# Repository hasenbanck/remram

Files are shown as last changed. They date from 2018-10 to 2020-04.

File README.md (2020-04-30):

# RemRam - 3D printer controller

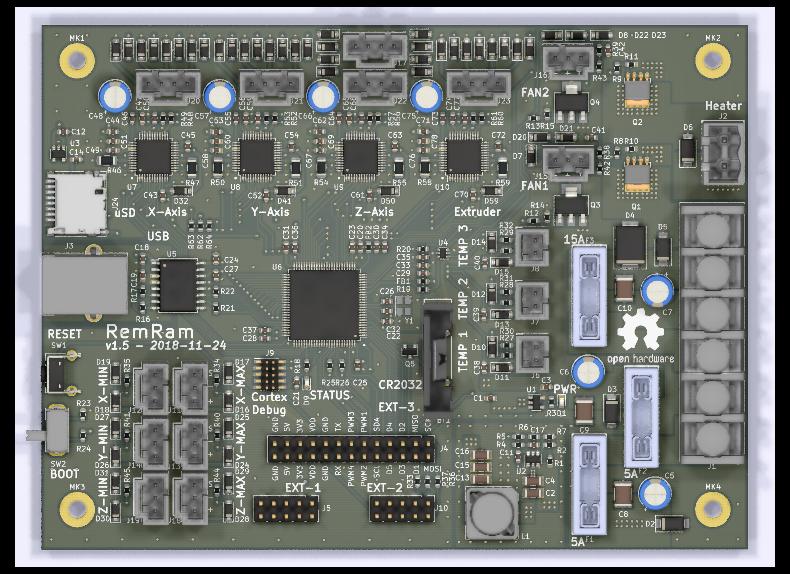
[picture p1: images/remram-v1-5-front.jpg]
RemRam v1.5


## Features

 * 32bit STM32F765VI
   * 216 MHz
   * 512 KBytes RAM
   * 2 MBytes flash
 * 4x TMC2130 stepper driver
   * stealthChop
   * spreadCycle
   * coolStep
   * stallGuard
 * 24V main power rail
   * heatbed output (15A)
   * heater output (5A)
   * stepper driver and logic (5A)
 * 5V secondary power rail (3A)
   * FAN1 and FAN2
 * 2x 3.3V tertiary power rail (2x 0.5A)
   * MCU power (IO)
   * SD card power
 * Robust connectors
 * Quality, high powered MOSFET
 * 4 layer board with single side component placement

## PCB design

Software used KiCad 5.0

### Alternative Parts

You can substitute the TPS5408 with a TPS5402. In this case you also need to replace R4 with a Zero Ohm resistor.

## Compiling the firmware

 1. [Install Arduino](https://www.arduino.cc/en/Main/Software)
 2. [Install the STM32 Core](https://github.com/stm32duino/wiki/wiki/Getting-Started)
 3. Optional for Serial over USB support: [Update the STM32 Core using the git repository](https://github.com/stm32duino/wiki/wiki/Using-git-repository)
 4. [Download the current git branch of Marlin 2.0](https://github.com/MarlinFirmware/Marlin/tree/bugfix-2.0.x)
 5. Open the Marlin project, select the "RemRam V1" board from the Marlin menue, edit the Marlin configuration file and build the project. You need to find the HEX or BIN file that Arduino creates and flash the firmware onto the board (See: "How to flash the firmware").

## Configure Marlin

These are the board specific ```Configuration.h``` changes:
```C
#define SERIAL_PORT 1 // 1 = UART connection on EXT3
                      // -1 = Serial over USB (see: Virtual COM Port Support (Serial over USB))
                      // You can also configure SERIAL_PORT_2

#define BAUDRATE 115200 // 115200 for UART on EXT3
                        // 1000000 for Serial over USB

#define MOTHERBOARD BOARD_REMRAM_V1

#define X_DRIVER_TYPE  TMC2130
#define Y_DRIVER_TYPE  TMC2130
#define Z_DRIVER_TYPE  TMC2130
#define E0_DRIVER_TYPE TMC2130

#define ENDSTOP_INTERRUPTS_FEATURE

#define SDSUPPORT
```

These are the board specific ```Configuration_adv.h``` changes:
```C
#define MINIMUM_STEPPER_DIR_DELAY 20
#define MINIMUM_STEPPER_PULSE 0
#define MAXIMUM_STEPPER_RATE 400000

#if HAS_TRINAMIC

  // You can change ever value EXCEPT R_SENSE based on your setup.
  // Example values of my HEVO setup

  #define R_SENSE           0.12  // DO NOT CHANGE! Need to be 0.12 for RemRam V1
  #define HOLD_MULTIPLIER    0.3  // Scales down the holding current from run current
  #define INTERPOLATE       true  // Interpolate X/Y/Z_MICROSTEPS to 256

  #define X_CURRENT          750  // rms current in mA. Multiply by 1.41 for peak current.
  #define X_MICROSTEPS       256  // 0..256

  #define Y_CURRENT          750
  #define Y_MICROSTEPS       256

  #define Z_CURRENT          750
  #define Z_MICROSTEPS       256

  #define E0_CURRENT         400
  #define E0_MICROSTEPS      256

  #define STEALTHCHOP
  #define MONITOR_DRIVER_STATUS

  #if ENABLED(MONITOR_DRIVER_STATUS)
    #define CURRENT_STEP_DOWN     50  // [mA]
    #define REPORT_CURRENT_CHANGE
    #define STOP_ON_ERROR
  #endif

  #define SENSORLESS_HOMING // If you want to use sensorless homing

  #if ENABLED(SENSORLESS_HOMING) || ENABLED(SENSORLESS_PROBING)
    #define X_STALL_SENSITIVITY  2
    #define Y_STALL_SENSITIVITY  2
    #define Z_STALL_SENSITIVITY  2
  #endif

  #define TMC_DEBUG // Helpfull when setting up your system

#endif
```

```src/pins/pins_REMRAM_V1.h```
```C
// Use only one or the other (you could damage the hardware otherwise!)
#define SDSS               57   // Onboard SD card reader
//#define SDSS              9   // LCD SD card reader
```

Of course you need to aditionally change the configuration files based on your particular printer setup.

## Virtual COM Port Support (Serial over USB)

Virtual COM Port (also known as VCOM or CDC) support will land in the "official" STM32 arduino core with version 1.5.0. If you want to use VCOM feature earlier, you can use the the [master branch of the offical core](https://github.com/stm32duino/Arduino_Core_STM32).

Have a look at the "[Update the STM32 Core using the git repository](https://github.com/stm32duino/wiki/wiki/Using-git-repository)" on how to update the STM32 arduino core with a custom git branch. You also have to select "CDC Full Speed" as USB interface inside Arduino to enable the CDC interface.

## External SD card reader

Most RepRapDiscount based LCD modules come with an integrated SD card reader. You can use this reader, but because this system is 3.3V based, the signal to noise ration is higher. Meaning you will need a much better connection between the LCD module and the board. Crappy ribbon cables won't do it in most cases. Dropping the SPI speed AND using shielded ribbon cables is most likely needed to get a good signal integrity.

You can't use the onboard SD card reader and the LCD card reader at the same time. DO NOT insert a SD card in both slots at the same time, because this could lead to a hardware failure.

## How to flash the firmware

Supported:

 * Using the Cortex Debug Header (SWD)
 * Using DFU over USB
 * Using UART on EXT-3 PIN 15 (TX) and PIN 16 (RX)

### Cortex Debug Header

You can use the Cortex Debug Header to program the STM32 firmware and do step-by-step debugging.

This board only support SWD. SWO is not routed to the header, since we had to use the
pin for a PWM output.

I personally use the SEGGER J-Link Edu Mini. But any 2€ Ebay flasher should work ("ST Link V2").
Please make sure that you have a adapter for the debug header!

The debug header is a 2x05 pin (1.27/0.05”).

### DFU (USB)

https://www.st.com/en/development-tools/stsw-stm32080.html

Please pay attention that you don't just flash the HEX/BIN file, but the special DFU image file (*.dfu) you need to create with the "DFU file manager" tool. DfuSe will let you happily flash a HEX/BIN file, but the board won't boot without a propper DFU file.

Please read the "UM0412" user manual you can find at the above link.

### UART

https://www.st.com/en/development-tools/flasher-stm32.html

## LICENSE

CERN OHL version 1.2

The files under PCB/packages3d are excluded from this license and are provided under fair use terms for this open-source project.

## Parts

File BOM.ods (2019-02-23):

Reference(s) | Value | Mft. Nr. | Digikey Nr. | Mouser Nr. | Qty | Notice | Footprint | Datasheet
BT1 | S8401-46 | S8401-46 | 952-1743-1-ND | 855-S8401-46 | 1 |  | custom-footprints:VBH2032-1 | https://www.mouser.de/datasheet/2/346/VBH2032-1_new-258024.pdf
C1, C3, C12, C14, C50, C59, C68, C77 | 10uF | GRM188R61A106KE69J | 490-14372-1-ND | 81-ZRB18AR61E106ME1L | 8 | Min. 10V | Capacitor_SMD:C_0603_1608Metric | ~
C11, C18, C19, C21, C22, C23, C24, C25, C27, C28, C31, C33, C34, C35, C38, C39, C40, C41, C42, C43, C44, C45, C49, C51, C52, C53, C54, C58, C60, C61, C62, C63, C67, C69, C70, C71, C72, C76, C78 | 100nF | C0603C104M5RACTU | 399-7845-1-ND | 80-C0603C104M5R | 39 | Min. 35V | Capacitor_SMD:C_0603_1608Metric | ~
C13, C15, C16 | 22uF | GRM319C80J226ME15D | 1276-3148-1-ND | 81-GRM319C80J226ME5D | 3 | Min. 10V | Capacitor_SMD:C_1206_3216Metric | ~
C17 | 75pF | GRM1885C1H750JA01D | 490-1424-1-ND | 81-GRM1885C1H750JA | 1 | Min. 10 V | Capacitor_SMD:C_0603_1608Metric | ~
C2 | 10uF | GRM319R6YA106KA12D | 490-12425-1-ND | 81-GRT31CC8YA106ME1L | 1 | Min. 35V | Capacitor_SMD:C_1206_3216Metric | ~
C20 | 4.7uF | GRM188R61A475ME15D | 490-10478-1-ND | 810-CGB3B1X5R1A475MC | 1 | Min. 10V | Capacitor_SMD:C_0603_1608Metric | ~
C26, C32 | 8pF | GCM1885C1H8R0DA16D | 490-14528-1-ND | 81-GCM1885C1H8R0DA6D | 2 | Min. 10V | Capacitor_SMD:C_0603_1608Metric | ~
C29, C30 | 1uF | 885012206052 | 732-7971-1-ND | 710-885012106010 | 2 | Min. 10V | Capacitor_SMD:C_0603_1608Metric | ~
C36, C37 | 2.2uF | 885012106011 | 732-7908-1-ND | 710-885012106011 | 2 | Min. 10V | Capacitor_SMD:C_0603_1608Metric | ~
C4 | 100nF | C1206C104K5RACAUTO | 399-7009-1-ND | 80-C1206C104K5RAUTO | 1 | Min. 35V | Capacitor_SMD:C_1206_3216Metric | ~
C46, C55, C64, C73 | 22nF | 885012206091 | 732-8009-1-ND | 710-885012206091 | 4 | Min. 50V | Capacitor_SMD:C_0603_1608Metric | ~
C47, C56, C65, C74 | 470nF | 885012106008 | 732-7905-1-ND | 710-885012106008 | 4 | Min. 10V | Capacitor_SMD:C_0603_1608Metric | ~
C5, C6, C7, C48, C57, C66, C75 | 100uF | 860020573008 | 732-8942-1-ND | 710-860020573008 | 7 | Min. 35V | Capacitor_THT:CP_Radial_D6.3mm_P2.50mm | https://eu.mouser.com/datasheet/2/293/e-uvz-1219460.pdf
C8, C9, C10 | 100nF | C4532X7R2J104K230KA | 445-2300-1-ND | 603-CC812KKX7R9BB104 | 3 | Min. 35V | Capacitor_SMD:C_1812_4532Metric | ~
D1 | LTST-C194KGKT | LTST-C194KGKT | 160-1834-1-ND | 859-LTST-C194KGKT | 1 |  | LED_SMD:LED_0603_1608Metric | ~
D2, D3 | SMAJ28A | SMAJ28A-13-F | SMAJ28A-FDICT-ND | 621-SMAJ28A-13-F | 2 |  | Diode_SMD:D_SMA | https://www.mouser.de/datasheet/2/240/Littelfuse_TVS_Diode_SMAJ_Datasheet.pdf-540740.pdf
D32, D33, D34, D35, D36, D37, D38, D39, D40, D41, D42, D43, D44, D45, D46, D47, D48, D49, D50, D51, D52, D53, D54, D55, D56, D57, D58, D59, D60, D61, D62, D63, D64, D65, D66, D67 | S310FA | S310FA | S310FACT-ND | 512-S310FA | 36 |  | Diode_SMD:D_SOD-123 | https://www.mouser.com/ds/2/149/S310FA-888043.pdf
D4 | S3A-13-F | S3A-13-F | S3A-FDICT-ND | 621-S3A-F | 1 |  | Diode_SMD:D_SMC | https://www.mouser.de/datasheet/2/115/ds16005-37880.pdf
D5, D6 | SK310A-LTP | SK310A-LTP | SK310A-LTPMSCT-ND | 833-SK310A-LTP | 2 |  | Diode_SMD:D_SMA | https://www.mouser.de/ProductDetail/Micro-Commercial-Components-MCC/SK310A-TP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
D7, D8, D10, D11, D12, D13, D14, D15, D16, D17, D18, D19, D20, D21, D22, D23, D24, D25, D26, D27, D28, D29, D30, D31 | BAT54GWJ | BAT54GWJ | 1727-7328-1-ND | 841-BAT54GWJ | 24 |  | Diode_SMD:D_SOD-123 | https://www.mouser.de/datasheet/2/916/BAT54GW-1318921.pdf
D9 | LTST-C194KSKT | LTST-C194KSKT | 160-1836-1-ND | 859-LTST-C194KSKT | 1 |  | LED_SMD:LED_0603_1608Metric | ~
F1, F2, F3 | 3557-2 | 3557-2 | 36-3557-2-ND | 534-3557-2 | 3 |  | custom-footprints:KEYSTONE-FUSE-3557-2 | https://www.mouser.de/datasheet/2/215/557-2-744839.pdf
FB1, FB2 | MPZ1608S221A | MPZ1608S221A | 445-1565-1-ND | 810-MPZ1608S221A | 2 |  | Resistor_SMD:R_0603_1608Metric | https://www.mouser.de/datasheet/2/400/eads_commercial_power_mpz1608_en-923650.pdf
J1 | 4DB-P108-06 | 4DB-P108-06 | A98476-ND | 571-214376679 | 1 | Alternative OSTYK42106030? | custom-footprints:4DB-P108-06
J11, J12, J13, J14, J15, J16, J18, J19 | 70543-0002 | 70543-0002 | WM4801-ND | 538-70543-0002 | 8 |  | custom-footprints:70543-0002 | ~
J17, J20, J21, J22, J23 | 70543-0003 | 70543-0003 | WM4802-ND | 538-70543-0003 | 5 |  | custom-footprints:70543-0003 | https://www.mouser.de/ProductDetail/Molex/70543-0003
J2 | 039531-1002 | 039531-1002 | WM7837-ND | 538-39531-1002 | 1 |  | custom-footprints:39531-1002 | ~
J24 | DM3D-SF | DM3D-SF | HR1941CT-ND | 798-DM3D-SF | 1 |  | custom-footprints:microSD_HC_Hirose_DM3D-SF | ~
J3 | 67068-8000 | 67068-8000 | WM17113-ND | 538-67068-8000 | 1 |  | custom-footprints:67068-8000 | https://www.mouser.de/datasheet/2/276/0670688000_IO_CONNECTORS-172066.pdf
J4 | Conn_02x13_Odd_Even | 67997-426HLF | 609-3246-ND | 649-67997-426HLF | 1 |  | custom-footprints:PinHeader_2x13_P2.54mm_Vertical | ~
J5, J10 | Conn_02x05 | 67997-210HLF | 609-3236-ND | 649-67997-210HLF | 2 | Buy them cheap on aliexpress, ebay or amazon | Connector_PinHeader_2.54mm:PinHeader_2x05_P2.54mm_Vertical
J6, J7, J8 | 70543-0001 | 70543-0001 | WM4800-ND | 538-70543-0001 | 3 |  | custom-footprints:70543-0001 | https://www.mouser.de/ProductDetail/Molex/50-57-9402
J9 | 20021121-00010C4LF | 20021121-00010C4LF | 609-3695-1-ND | 649-202112100010C4LF | 1 |  | custom-footprints:PinHeader_2x05_P1.27mm_Vertical | https://www.mouser.de/datasheet/2/445/6220xx21121-542317.pdf
L1 | 18uH | 7447798181 | 732-2417-1-ND | 710-7447798181 | 1 |  | custom-footprints:L_Wuerth_WE-PDF | https://www.mouser.com/datasheet/2/445/7447798181-539715.pdf
Q1, Q2 | PSMN1R2-30YLC,115 | PSMN1R2-30YLC,115 | 1727-5295-1-ND | 771-PSMN1R230YLC115 | 2 | Alternatives: PSMN1R8-40YLC,115; PSMN1R3-30YL,115 | custom-footprints:SOT-669_LFPAK_ThermalVias-1 | https://assets.nexperia.com/documents/data-sheet/PSMN1R2-30YLC.pdf
Q3, Q4 | BUK9840-55 | BUK9840-55/CUX | 1727-2227-1-ND | 771-BUK9840-55/CUX | 2 |  | Package_TO_SOT_SMD:SOT-223-3_TabPin2 | https://www.mouser.de/datasheet/2/916/BUK9840-55-1320170.pdf
Q5 | IRLML6401 | IRLML6401TRPBF | IRLML6401PBFCT-ND | 942-IRLML6401TRPBF | 1 | Alternative: SI2333DS-T1-E3 | Package_TO_SOT_SMD:SOT-23 | https://www.infineon.com/dgdl/irlml6401pbf.pdf?fileId=5546d462533600a401535668b96d2634
R1 | 511k | ERJ-3EKF5113V | P511KHCT-ND | 667-ERJ-3EKF5113V | 1 |  | Resistor_SMD:R_0603_1608Metric | ~
R6, R10, R11, R14, R15 | 100k | CRCW0603100KFKEAC | 541-3950-1-ND | 71-CRCW0603100KFKEAC | 5 |  | Resistor_SMD:R_0603_1608Metric | ~
R8, R9, R12, R13, R16, R17, R21, R22, R33, R36, R37 | 100 | RC0603FR-7W100RL | YAG3561CT-ND | 603-RC0603FR-7W100RL | 11 |  | Resistor_SMD:R_0603_1608Metric | ~
R3, R18, R19, R20, R34, R35, R40, R41, R44, R45 | 1k | RC0603JR-7W1KL | YAG2323CT-ND | 603-RC0603JR-7W1KL | 10 |  | Resistor_SMD:R_0603_1608Metric | ~
R2 | 105k | ERJ-3EKF1053V | P105KHCT-ND | 667-ERJ-3EKF1053V | 1 |  | Resistor_SMD:R_0603_1608Metric | ~
R23, R24, R48, R49, R52, R53, R56, R57, R60, R61, R62, R63, R64 | 47k | CR0603-FX-4702ELF | CR0603-FX-4702ELFTR-ND | 652-CR0603FX-4702ELF | 13 |  | Resistor_SMD:R_0603_1608Metric | ~
R25, R26 | 10k | AC0603FR-0710KL | P10.0KHCT-ND | 603-AC0603FR-0710KL | 2 |  | Resistor_SMD:R_0603_1608Metric | ~
R27, R28, R29, R30, R31, R32, R38, R39, R42, R43, R65 | 4.7k | AC0603JR-074K7L | YAG3676CT-ND | 603-AC0603JR-074K7L | 11 |  | Resistor_SMD:R_0603_1608Metric | ~
R4 | 2k | CRCW06032K00FKEAC | 541-3953-1-ND | 71-CRCW06032K00FKEAC | 1 | Option when using TPS54302: ERJ-3GEY0R00V | Resistor_SMD:R_0603_1608Metric | ~
R46, R47, R50, R51, R54, R55, R58, R59 | 0.12 | ERJ-8RSJR12V | P.12PCT-ND | 667-ERJ-8RSJR12V | 8 |  | Resistor_SMD:R_1206_3216Metric | https://www.mouser.de/ProductDetail/IRC-TT-Electronics/LRC-LR1206LF-01-R120-F
R5 | 49.9 | ERJ-3EKF49R9V | P49.9HCT-ND | 667-ERJ-3EKF49R9V | 1 |  | Resistor_SMD:R_0603_1608Metric | ~
R7 | 13.3k | AC0603FR-0713K7L | P13.7KHCT-ND | 603-AC0603FR-0713K7L | 1 |  | Resistor_SMD:R_0603_1608Metric | ~
SW1 | PTS645VL39-2 | PTS645VL392LFS | CKN9103-ND | 611-PTS645VL392 | 1 |  | Button_Switch_THT:SW_Tactile_SPST_Angled_PTS645Vx39-2LFS | https://www.mouser.de/datasheet/2/60/-1131575.pdf
SW2 | OS102011MA1QN1 | OS102011MA1QN1 | CKN9559-ND | 611-OS102011MA1QN1 | 1 |  | custom-footprints:SW_CuK_OS102011MA1QN1_SPDT_Angled | ~
U1, U3 | AP7365-33WG-7 | AP7365-33WG-7 | AP7365-33WG-7DICT-ND | 621-AP7365-33WG-7 | 2 |  | Package_TO_SOT_SMD:SOT-23-5 | https://www.mouser.de/datasheet/2/115/AP7365-86154.pdf
U7, U8, U9, U10 | TMC2130-TA | TMC2130-TA-T | 1460-1186-1-ND |  | 4 | Not available at Mouser | custom-footprints:TQFP-48-1EP_7x7mm_P0.5mm_EP4.8x4.8mm-Heatsink | https://www.trinamic.com/fileadmin/assets/Products/ICs_Documents/TMC2130_datasheet.pdf
U2 | TPS54308 | TPS54308DDCT | 296-47881-1-ND | 595-TPS54308DDCT | 1 | Alternative: TOS54302 (Attention R4!) | Package_TO_SOT_SMD:SOT-23-6 | http://www.ti.com/lit/ds/symlink/tps54308.pdf
U4 | SN74LVC2G17DCKR | SN74LVC2G17DCKR | 296-13013-1-ND | 595-SN74LVC2G17DCKR | 1 |  | Package_TO_SOT_SMD:SOT-363_SC-70-6 | http://www.ti.com/lit/sg/scyt129e/scyt129e.pdf
U5 | ADUM4160 | ADUM4160 | ADUM4160BRIZ-RLCT-ND | 584-ADUM4160BRWZ-R | 1 |  | Package_SO:SOIC-16W_7.5x10.3mm_P1.27mm | http://www.analog.com/media/en/technical-documentation/data-sheets/ADuM4160.pdf
U6 | STM32F765VIT6 | STM32F765VIT6 | 497-16631-ND | 511-STM32F765VIT6 | 1 |  | custom-footprints:TQFP-100_14x14mm_P0.5mm | http://www.st.com/en/microcontrollers/stm32f765vi.html
Y1 | TSX-3225 24.0000MF15X-AC3 | TSX-3225 24.0000MF15X-AC3 | SER3635CT-ND | 732-TX325-24F15X-AC3 | 1 |  | Crystal:Crystal_SMD_SeikoEpson_TSX3225-4Pin_3.2x2.5mm | https://www5.epsondevice.com/en/products/crystal_unit/tsx3225.html

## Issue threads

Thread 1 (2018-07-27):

Write the STM32F7 HAL for Marlin 2.0

hasenbanck, 2018-07-27:
Even though there is already a STM32F7 HAL in Marlin 2.0 it is based on an unmaintained Arduino driver (https://github.com/danieleff/STM32GENERIC).

We should use the official arduino core (https://github.com/stm32duino/Arduino_Core_STM32) for the HAL. A current implementation is available (https://github.com/hasenbanck/Arduino_Core_STM32). It should move into upstream "soon".

Since the current STM32F7 HAL in Marlin is pretty board specific and can be highly simplified using the official Arduino core from ST, we should replace the current STM32F7 HAL in the long run. Right now it might be best to simply open a new HAL folder (STM32F7ng?).

hasenbanck, 2018-07-27:
It seems that another developer ported the F4 HAL for the official arduino core. We should use his code and maybe even consider making a unified HAL altogether.

https://github.com/ghent360/Marlin/tree/bugfix-2.0.x/Marlin/src/HAL/HAL_STM32F4

hasenbanck, 2018-07-27:
Forget this. The official F4 HAL is already ported for the official core.

hasenbanck, 2018-07-28:
I finished writing the HAL and board definition for Marlin 2.0.

https://github.com/hasenbanck/Marlin/commit/7cdb6b6f9d40818a396b762b27f7448407c70da5

Open issues:
 * Official Arduino Core doesn't support CDC yet (Serial over USB), so an external USB to TTL adapter is needed (Using USART1).
 * We need to be able to configure the timers (The borg used timer 5 and 7, we use 2 and 5 etc)
 * Watchdog support not yet in the Arduino Core. Will be implemented with 1.3.1 (PR already finished)

Closed 2018-07-28.

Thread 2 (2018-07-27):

Write the board definition for Marlin 2.0

hasenbanck, 2018-07-27:
When the STM32F7 HAL is finished, we should write the board definition for RemRam 1.*.

hasenbanck, 2018-07-28:
Implemented in https://github.com/hasenbanck/Marlin/commit/7cdb6b6f9d40818a396b762b27f7448407c70da5

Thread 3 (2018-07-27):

Upstream the RemRam board variant for Arduino_Core_STM32

hasenbanck, 2018-07-27:
Upstream https://github.com/hasenbanck/Arduino_Core_STM32 to https://github.com/stm32duino/Arduino_Core_STM32

hasenbanck, 2018-07-27:
Opened PR: stm32duino/Arduino_Core_STM32/pull/287

hasenbanck, 2018-10-03:
Implemnted with https://github.com/stm32duino/Arduino_Core_STM32/commit/c5563f3448e856d535accfcfd3cf78687bc02d5e

Closed 2018-10-03.

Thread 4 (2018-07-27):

Upstream the HAL and board definition in Marlin 2.0

hasenbanck, 2018-07-27:
Upstream our HAL and board definition in Marlin 2.0.

hasenbanck, 2018-10-03:
Implemented in https://github.com/MarlinFirmware/Marlin/commit/348004c34fc58dbcb5eb697b4d3dc598628e2adf

Closed 2018-10-03.

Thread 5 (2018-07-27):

Write build instructions for RemRam 1.1.

hasenbanck, 2018-07-27:
We need to write Wiki entries for the build process of a RemRam v1.1 board with pictures and debug information.

gauix4, 2018-10-25:
Hello
so if I understand correctly we can use the whole series of STM32F7
I have plenty of STM32F767ZIT6

hasenbanck, 2018-10-25:
No, you can't use the STM32F767ZIT6 instead. It's 144 pin, whereas the STM32F765VIT6 the design is based on has 100 pins.

The variant definition in the Ardunio core is also based on the STM32F765VIT6, so you would need to write a whole new variant if you want to use another MCU (which would need to be pin / configuration compatible). And the Marlin stuff has also STM32F765VIT6 specific stuff.

So no ... you really can't use a STM32F767ZIT6 instead.

gauix4, 2018-10-25:
it exists in version also LQFP100 is what I have ^^

hasenbanck, 2018-10-25:
No, the STM32F767ZI is the model number for LQFP144. LQFP100 for the STM32F767 has the part number STM32F767VI and STM32F767VG.

If you mean those two, then the answer is still: No, you can't just replace them. You would need to check the configuration with STM32Cube MX (the current configuration is provided with the sources) to make sure that it's really pin / configuration compatible.

Then you would also need to write your own board definition file for the Arduino core. And you would need also to adjust the Marlin sources to support your MCU with this board.

If you are willed to do that, then you could try doing it. But it's not supported by this design and the current software (Core and Marlin).

gauix4, 2018-10-25:
So I will still order the STM32F765VIT6 ^^

hasenbanck, 2018-10-25:
Yes, please stick to the BOM.

gauix4, 2018-10-25:
I could always help develop the project a bit more

hasenbanck, 2018-10-25:
Help is always welcome, but RemRam starting from 1.3 will stay backward
compatible. So you would need to keep that in mind.

The software side only lacks the CDC support in the core and I already made
a merge request for that. But of course it could need more work.

V1.3 is also not tested yet well. So there could be a v1.4 if people find
bugs in the design.

I personally will only support it. My main development resources as of
right now move into the heteromycin project of mine that you can also find
on GitHub, were I take a more radical approach from the lessons I learned
with RemRam. You are also welcome to help there.

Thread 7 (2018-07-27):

Write a guide on how to upload the firmware

hasenbanck, 2018-07-27:
We support multiple ways on how to upload a firmware (DFU, Serial, SWD). We need to write a guide for all of them.

G-Pereira, 2018-10-12:
I am looking to program it by hooking up a raspberry pi to the UART pins, can you explain how can I do that? I find odd not having to connect the STM32 reset pin to my RPi or the RTS signal.

hasenbanck, 2018-10-12:
Simply flip the boot switch and hit the reset button. Then the bootloader will start and you can flash the board using the TX/RX pins and a tool such as stm32flash. Be sure to use the current git master, since the 0.5 version doesn't support the STM32F765VI.

Closed 2019-01-12.

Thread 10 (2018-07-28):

Resolve timer configuration problem

hasenbanck, 2018-07-28:
We need to find a way to make timer configurable inside the F7 HAL. There is a upstream issue for this kinda topic:
https://github.com/stm32duino/Arduino_Core_STM32/issues/222

But this needs to be handled inside Marlin anyhow. We need to sync with other Marlin 32bit STM developers.

hasenbanck, 2018-10-03:
Solved and upstream with the new STM32 HAL in Marlin.

Closed 2018-10-03.

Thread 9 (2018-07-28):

Implement CDC / Virtual COM Port

hasenbanck, 2018-07-28:
Once the official Arduino core implements CDC, we need to add support for this in Marlin.

Upstream issue to track:
https://github.com/stm32duino/Arduino_Core_STM32/issues/222

hasenbanck, 2018-10-03:
Work started with https://github.com/stm32duino/Arduino_Core_STM32/pull/344

hasenbanck, 2019-01-12:
CDC support has landed upstream in the master branch and will be included in version 1.5

Closed 2019-01-12.

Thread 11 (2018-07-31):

SD Card communication is corrupt

hasenbanck, 2018-07-31:
On my development board I can't read SD card content from a RepRapDiscount Smart LCD.

The software implementation seems okay and the debugger shows me, that we receive corrupt data. Sending commands over SPI to the SD card seems working and fine. Receiving data from the SD card seems broken. Every 7. and 8. byte seems corrupt in a totally predictable and non-random manner (I attached an oscilloscope view with the CLK and MISO signals while reading one 512 byte sector). The test data was 512 byte of 0xFF. 512 byte of 0x00 would result in the 7. byte = 0xf and 8. byte = 0x4 pattern.
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

Random noise seems very, very unlikely. The signal looks fine and I already went down in speed considerably. The most likely current culprit is a bad behaving SPI slave on the bus (one of the TMC2130 might send a SPI_STATUS packet?).

I already tried different SD cards and also two different LCD controller.

hasenbanck, 2018-07-31:
When deasserting the SD card before reading, the MISO stays high. So it seems there is no misbehaving SPI slave...

Further investigations needed.

hasenbanck, 2018-07-31:
Using another STM32 devboard, I could read from the same SD card successfully. When lowering the CPU clockspeed, the faulty data seem to disapear. But mounting is still not possible.

Faulty MCU? Too noisy? Bug?

Running optimization on the code seem to make things generally worse (-0s, 02 etc).

hasenbanck, 2018-08-01:
I wrote a simple memory test, which I ran for a couple of minutes that fills 256KB of the RAM with patterns / antipatterns and compares them with the expected result, to find possible corruptions in the operation of the MCU.

The test worked flawless. So a general power / stability problem with the MCU seems not realistic.

hasenbanck, 2018-08-02:
It seems that I'm currently hunting software bug. I think it's highly likely that the current combination of Marlin's SD-SPI Mode code, the STM32 arduino core and my HAL is the culpit. I have ordered a logic analyzer to debug this problem.

hasenbanck, 2018-08-03:
Logic analyzer did't arrived yet, but I tested another MicroSD card reader over SPI and that thing worked flawlessly...

Then I tested another SD Card reader of another brand, and it had the same errors as my RepRap Discount Smart / Graphic controllers.

hasenbanck, 2018-08-25:
After some more testing, the problem seem to result from minor quality ribbon cables. When using better ribbon cable, the SD card communication seem to work fine. For the v1.2 design I added series resistors to the SPI pins to get better noise handling. Hopefully this will result in a better handling of SD card communication.

Closed 2018-08-25.

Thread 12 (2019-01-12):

Writing to SD card overCDC/VCOM doesn't work

hasenbanck, 2019-01-12:
Currently we can't write to SD card using pronterface/pronsole. It will try to create/open a file on the SD card and will fail doing. Reading from a onboard SD card works fine.

Things we tried but didn't fix the issue:
 * Lower the baud rate of the CDC / VCOM port
 * Lowering the SPI speed
 * Using either an external or the onboard sd card reader

This bug needs further testing / investigation to find the possible cause.

hasenbanck, 2019-01-12:
Further testing revealed:
 * Saving a file over UART to SD card also doesn't work
 * Using M928 (saving a logfile to SD card) also doesn't work

Maybe the error lies in the marlin HAL for the STM32.

hasenbanck, 2019-01-12:
@ktand Is the M928 working on your ARMED board using an external SD card reader? i want to know this, because if it is working, then my board design would be the cause. If it doesn't, it would mean the cause lies inside the STM32 HAL inside Marlin.

ktand, 2019-01-12:
I can check later today.

hasenbanck, 2019-01-12:
@ktand Thank you very much!

ktand, 2019-01-12:
@hasenbanck Doesn't seem to work on my board either, so I guess there is some more work to be done in the STM32 Marlin HAL. I can however print from SD card but not upload files to it.

hasenbanck, 2019-01-12:
@ktand Thank you for testing. I'm a little bit relieved that it's not hardware related and that it seems to be the STM32 Marlin HAL. I will poke around and will look for the issue in the next days.

And yes, reading works fine on my end too. SPI writing also works, since my TMC2130 drivers are getting configured. So it seems to be related to either the block writing of data or maybe the FAT filesystem code (?).

ktand, 2019-01-13:
@hasenbanck I have identified the problem and created a PR, see https://github.com/MarlinFirmware/Marlin/pull/12896

ktand, 2019-01-13:
@hasenbanck Made an error in my previous Marlin PR... Created a new one: https://github.com/MarlinFirmware/Marlin/pull/12897

hasenbanck, 2019-01-13:
@ktand Thank you very much! You saved ma a lot of time.

leseaw, 2019-01-17:
@ktand @hasenbanck  fix isnt working :( worse than before, now not even reading possible.

hasenbanck, 2019-01-17:
@leseaw Rebased my config to the newest bugfix 2.0 master. Seems to work fine on my end for the reading. Writing still seems bugged after some kilobytes, but that is still under investigation like already said some days before.

hasenbanck, 2019-01-17:
Changing the SPI mode from 0 to 3 solved all of my writing problems. I will catch some sleep and think about this over the weekend.

hasenbanck, 2019-01-19:
Changing to SPI mode 3 shouldn't be necessary, since all devices on the bus are mode 0 devices. I changed back the mode 0 and measured the MOSI, MISO and SCLK lines. The resistance of the MOSI and MISO lines were 27k, so it seem that the STM32 also has PU activated even when not running. I removed the extra PU to remove some variables in the testing. The SPI speed is also greatly reduced while testing.

I then used my oscilloscope to measure the SPI bus (Blue= SCLK, RED = MOSI, YELLOW = MISO):

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

These are clearly a SPI mode 0 signals. The timing of the signal also seems fine. There is an odd spike before writing a byte on the MOSI line (that seem to bleed in the SCLK line).

I couldn't measure the burst writing (that is failing) yet. But if these odd spikes are there while bursting, this could explain the errors we are seeing right now. I will try to add some capacitor values that could act as a filter. I'm also not sure where these spikes could originate. The TMC drivers are deactivated while testing this bug.

hasenbanck, 2019-01-19:
Here is a capture with a 1nF on the MISO and MOSI line (pretty aggressive). I tested this with one quarter SPI speed. Full speed won't work since the filtering would be too aggressive. The burst writing seems clean and fine.

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

I observed some off spikes on the CLK line.

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

No clue were this spikes come from, if it could count as "HIGH" for the SD card and why this should or even could influence only the SD writing.

I try to capture the SPI bus traffic with a logic analyzer next.

hasenbanck, 2019-01-20:
Attached a logic analyzer and took a dump of the write operation to SD card (Pulseview):

[pulseview.zip](https://github.com/hasenbanck/remram/files/2776477/pulseview.zip)

Overall the dump seems fine. The SCLK, MISO and MOSI register cleanly and it seems the little "noise spikes" shown above are not a problem (at least for the logic analyser). I don't have a deep insight into the SPI based SD card protocol, so I can't comment on that yet. I also don't know how well the SPI SD card protocol is implemented into Pulseview.

I will try to add a very small capacitor on SCLK line to filter out those little spikes, just to be safe. Would be great if there would be other F7 designs in Marlin for test against, but the only other design is currently dormant.

Those little spikes for now are my best target to investigate further. After I filtered them out and the SD card writing shouldn't work, I will go deeper into the overall SD card operation / protocol. The random nature of the problem and the clean output that it produces (the gcode fragments that are written on the card are clean and don't contain any ASCII garbage as you might expect on a noise/corrupt bus) make it rather hard to pinpoint a likely culprit.

hasenbanck, 2019-01-22:
A user on discord debugged the problem separately and came to the conclusion, that the noise spike comes from initializing the SPI device again and again when doing byte write transactions by Marlin.

The spike is the CLK line pulling up on SPI device re-init. The "big" spikes are happening, when there is an interrupt firing while the SPI device is initializing: Then it will have enough time to get pulled up to logic high.

A PD resistor on the CLK line of 47k seem to work (tested by the other user, but not by me yet). I will have to try it myself, maybe this is a good workaround for now.

I don't know why Marlin is calling ```spiInit()``` as often as it does right now. But it seems that at least on my device (STM32F765VI) this isn't really a great idea, since the SPI CLK line behavior described above (since the CS for the currently active device is asserted high).

So besides adding a weak PU (47k) there's maybe the need to add a fix in the STM32 HAL. Following options spring to my mind:

 1. Prevent Marlin to call spiInit() multiple times. Maybe we store the current configuration and only apply a new configuration, if it differs from the old one.
 2. Disable interrupts when inside the spiInit() function. But I don't know if this would be enough for all cases.

@ktand I don't know why you are not affected from this behavior. Maybe the F4 behaves differently on SPI reinit (or maybe you have a PD on the CLK line, but I doubt that).

hasenbanck, 2019-01-23:
47k is too low. 4.7k is needed as a PD.

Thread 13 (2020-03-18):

Marlin 2.0 no run

dennis0212, 2020-03-18:
Hello,

REMRAM no funtion with 2.0.5. Error with REPRAP FULL DISPLAY.  Start board and now watchdog LED blinked. Have you a Firmware for this Board?

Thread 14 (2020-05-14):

Marlin will not compile for RemRam

myval, 2020-05-14:
Hi,
Just got RemRam V1 board and have been trying to compile Marlin 2.0 and/ or 2.1dev but no luck.
I get these errors:
`
Marlin\src\HAL\STM32_F4_F7\HAL_SPI.cpp: In function 'void spiRead(uint8_t*, uint16_t)':
Marlin\src\HAL\STM32_F4_F7\HAL_SPI.cpp:125:9: error: 'class SPIClass' has no member named 'dmaTransfer'; did you mean 'transfer'?
  125 |     SPI.dmaTransfer(0, const_cast<uint8_t*>(buf), nbyte);
      |         ^~~~~~~~~~~
      |         transfer
Marlin\src\HAL\STM32_F4_F7\HAL_SPI.cpp: In function 'void spiSendBlock(uint8_t, const uint8_t*)':
Marlin\src\HAL\STM32_F4_F7\HAL_SPI.cpp:157:9: error: 'class SPIClass' has no member named 'dmaSend'
  157 |     SPI.dmaSend(const_cast<uint8_t*>(buf), 512);
Compiling .pio\build\STM32F7\src\src\HAL\shared\eeprom_i2c.cpp.o
      |         ^~~~~~~
Compiling .pio\build\STM32F7\src\src\HAL\shared\eeprom_spi.cpp.o
*** [.pio\build\STM32F7\src\src\HAL\STM32_F4_F7\HAL_SPI.cpp.o] Error 1
In file included from e:\documents\github\marlin-2.0.x\marlin\src\hal\hal.h:26,
                 from e:\documents\github\marlin-2.0.x\marlin\src\inc\marlinconfig.h:30,
                 from Marlin\src\HAL\shared\backtrace\../../../core/serial.h:24,
                 from Marlin\src\HAL\shared\backtrace\backtrace.cpp:29:
Marlin\src\HAL\shared\backtrace\backtrace.cpp: In function 'bool UnwReportOut(void*, const UnwReport*)':
e:\documents\github\marlin-2.0.x\marlin\src\hal\stm32_f4_f7\hal.h:55:21: error: 'SerialUART1' was not declared in this scope; did you mean 'SerialLP1'?
   55 |   #define MYSERIAL0 SerialUART1
      |                     ^~~~~~~~~~~
Marlin\src\HAL\shared\backtrace\../../../core/serial.h:62:40: note: in expansion of macro 'MYSERIAL0'
   62 |   #define SERIAL_OUT(WHAT, V...) (void)MYSERIAL0.WHAT(V)
      |                                        ^~~~~~~~~
Marlin\src\HAL\shared\backtrace\../../../core/serial.h:88:27: note: in expansion of macro 'SERIAL_OUT'
   88 | #define _CHAR_1(c)        SERIAL_OUT(write, c)
      |                           ^~~~~~~~~~
Marlin\src\HAL\shared\backtrace\../../../core/serial.h:86:27: note: in expansion of macro '_CHAR_1'
   86 | #define __CHAR_N(N,V...)  _CHAR_##N(V)
      |                           ^~~~~~
Marlin\src\HAL\shared\backtrace\../../../core/serial.h:87:27: note: in expansion of macro '__CHAR_N'
   87 | #define _CHAR_N(N,V...)   __CHAR_N(N,V)
      |                           ^~~~~~~~
Marlin\src\HAL\shared\backtrace\../../../core/serial.h:99:27: note: in expansion of macro '_CHAR_N'
   99 | #define SERIAL_CHAR(V...) _CHAR_N(NUM_ARGS(V),V)
      |                           ^~~~~~~
Marlin\src\HAL\shared\backtrace\backtrace.cpp:38:3: note: in expansion of macro 'SERIAL_CHAR'
   38 |   SERIAL_CHAR('#'); SERIAL_PRINT(*p, DEC); SERIAL_ECHOPGM(" : ");
      |   ^~~~~~~~~~~
*** [.pio\build\STM32F7\src\src\HAL\shared\backtrace\backtrace.cpp.o] Error 1`

I have searched the net but no luck to find solution.
Thanks
Josef

myval, 2020-05-14:
>
Marlin\src\HAL\STM32_F4_F7\HAL_SPI.cpp: In function 'void spiRead(uint8_t*, uint16_t)':
Marlin\src\HAL\STM32_F4_F7\HAL_SPI.cpp:125:9: error: 'class SPIClass' has no member named 'dmaTransfer'; did you mean 'transfer'?
  125 |     SPI.dmaTransfer(0, const_cast<uint8_t*>(buf), nbyte);
      |         ^~~~~~~~~~~
      |         transfer
Marlin\src\HAL\STM32_F4_F7\HAL_SPI.cpp: In function 'void spiSendBlock(uint8_t, const uint8_t*)':
Marlin\src\HAL\STM32_F4_F7\HAL_SPI.cpp:157:9: error: 'class SPIClass' has no member named 'dmaSend'
  157 |     SPI.dmaSend(const_cast<uint8_t*>(buf), 512);
Compiling .pio\build\STM32F7\src\src\HAL\shared\eeprom_i2c.cpp.o
      |         ^~~~~~~
Compiling .pio\build\STM32F7\src\src\HAL\shared\eeprom_spi.cpp.o
*** [.pio\build\STM32F7\src\src\HAL\STM32_F4_F7\HAL_SPI.cpp.o] Error 1
In file included from e:\documents\github\marlin-2.0.x\marlin\src\hal\hal.h:26,
                 from e:\documents\github\marlin-2.0.x\marlin\src\inc\marlinconfig.h:30,
                 from Marlin\src\HAL\shared\backtrace\../../../core/serial.h:24,
                 from Marlin\src\HAL\shared\backtrace\backtrace.cpp:29:
Marlin\src\HAL\shared\backtrace\backtrace.cpp: In function 'bool UnwReportOut(void*, const UnwReport*)':
e:\documents\github\marlin-2.0.x\marlin\src\hal\stm32_f4_f7\hal.h:55:21: error: 'SerialUART1' was not declared in this scope; did you mean 'SerialLP1'?
   55 |   #define MYSERIAL0 SerialUART1
      |                     ^~~~~~~~~~~
Marlin\src\HAL\shared\backtrace\../../../core/serial.h:62:40: note: in expansion of macro 'MYSERIAL0'
   62 |   #define SERIAL_OUT(WHAT, V...) (void)MYSERIAL0.WHAT(V)
      |                                        ^~~~~~~~~
Marlin\src\HAL\shared\backtrace\../../../core/serial.h:88:27: note: in expansion of macro 'SERIAL_OUT'
   88 | #define _CHAR_1(c)        SERIAL_OUT(write, c)
      |                           ^~~~~~~~~~
Marlin\src\HAL\shared\backtrace\../../../core/serial.h:86:27: note: in expansion of macro '_CHAR_1'
   86 | #define __CHAR_N(N,V...)  _CHAR_##N(V)
      |                           ^~~~~~
Marlin\src\HAL\shared\backtrace\../../../core/serial.h:87:27: note: in expansion of macro '__CHAR_N'
   87 | #define _CHAR_N(N,V...)   __CHAR_N(N,V)
      |                           ^~~~~~~~
Marlin\src\HAL\shared\backtrace\../../../core/serial.h:99:27: note: in expansion of macro '_CHAR_N'
   99 | #define SERIAL_CHAR(V...) _CHAR_N(NUM_ARGS(V),V)
      |                           ^~~~~~~
Marlin\src\HAL\shared\backtrace\backtrace.cpp:38:3: note: in expansion of macro 'SERIAL_CHAR'
   38 |   SERIAL_CHAR('#'); SERIAL_PRINT(*p, DEC); SERIAL_ECHOPGM(" : ");
      |   ^~~~~~~~~~~
*** [.pio\build\STM32F7\src\src\HAL\shared\backtrace\backtrace.cpp.o] Error 1

hasenbanck, 2020-05-14:
I don't actively develop for REMRAM anymore, so you are essentially on your own.

From what I can see in the logs your provided you are using the wrong HAL. The REMRAM board ist supposed to use the ```HAL/STM32``` HAL and not the ```HAL/STM_F4_F``` HAL.  Be sure to use the offical Arduino core:
https://github.com/stm32duino/Arduino_Core_STM32

Good luck.

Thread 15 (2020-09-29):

Marlin will not compile error: 'MYSERIAL' was not declared in this scope

kknox9713, 2020-09-29:
I'm trying to compile Marlin 2.0 for my skr mini 3 and I keep getting the following.
In file included from Marlin\src\HAL\shared\backtrace\backtrace.cpp:28:0:
Marlin\src\HAL\shared\backtrace\backtrace.cpp: In function 'bool UnwReportOut(void*, const UnwReport*)':
Marlin\src\HAL\shared\backtrace\../../../core/serial.h:68:40: error: 'MYSERIAL' was not declared in this scope
   #define SERIAL_OUT(WHAT, V...) (void)MYSERIAL.WHAT(V)
                                        ^
Marlin\src\HAL\shared\backtrace\../../../core/serial.h:94:27: note: in expansion of macro 'SERIAL_OUT'
 #define _CHAR_1(c)        SERIAL_OUT(write, c)
                           ^~~~~~~~~~
Marlin\src\HAL\shared\backtrace\../../../core/serial.h:92:27: note: in expansion of macro '_CHAR_1'
 #define __CHAR_N(N,V...)  _CHAR_##N(V)
Compiling .pio\build\STM32F103RC_btt_512K\src\src\HAL\shared\backtrace\unwmemaccess.cpp.o
                           ^~~~~~
Marlin\src\HAL\shared\backtrace\../../../core/serial.h:93:27: note: in expansion of macro '__CHAR_N'
 #define _CHAR_N(N,V...)   __CHAR_N(N,V)
                           ^~~~~~~~
Marlin\src\HAL\shared\backtrace\../../../core/serial.h:105:27: note: in expansion of macro '_CHAR_N'
 #define SERIAL_CHAR(V...) _CHAR_N(NUM_ARGS(V),V)
                           ^~~~~~~
Marlin\src\HAL\shared\backtrace\backtrace.cpp:37:3: note: in expansion of macro 'SERIAL_CHAR'
   SERIAL_CHAR('#'); SERIAL_PRINT(*p, DEC); SERIAL_ECHOPGM(" : ");
   ^~~~~~~~~~~
Marlin\src\HAL\shared\backtrace\../../../core/serial.h:68:40: note: suggested alternative: 'MSERIAL'
   #define SERIAL_OUT(WHAT, V...) (void)MYSERIAL.WHAT(V)
                                        ^
Marlin\src\HAL\shared\backtrace\../../../core/serial.h:94:27: note: in expansion of macro 'SERIAL_OUT'
 #define _CHAR_1(c)        SERIAL_OUT(write, c)
                           ^~~~~~~~~~
Marlin\src\HAL\shared\backtrace\../../../core/serial.h:92:27: note: in expansion of macro '_CHAR_1'
 #define __CHAR_N(N,V...)  _CHAR_##N(V)
                           ^~~~~~
Marlin\src\HAL\shared\backtrace\../../../core/serial.h:93:27: note: in expansion of macro '__CHAR_N'
 #define _CHAR_N(N,V...)   __CHAR_N(N,V)
                           ^~~~~~~~
Marlin\src\HAL\shared\backtrace\../../../core/serial.h:105:27: note: in expansion of macro '_CHAR_N'
 #define SERIAL_CHAR(V...) _CHAR_N(NUM_ARGS(V),V)
                           ^~~~~~~
Marlin\src\HAL\shared\backtrace\backtrace.cpp:37:3: note: in expansion of macro 'SERIAL_CHAR'
   SERIAL_CHAR('#'); SERIAL_PRINT(*p, DEC); SERIAL_ECHOPGM(" : ");
   ^~~~~~~~~~~
*** [.pio\build\STM32F103RC_btt_512K\src\src\HAL\shared\backtrace\backtrace.cpp.o] Error 1

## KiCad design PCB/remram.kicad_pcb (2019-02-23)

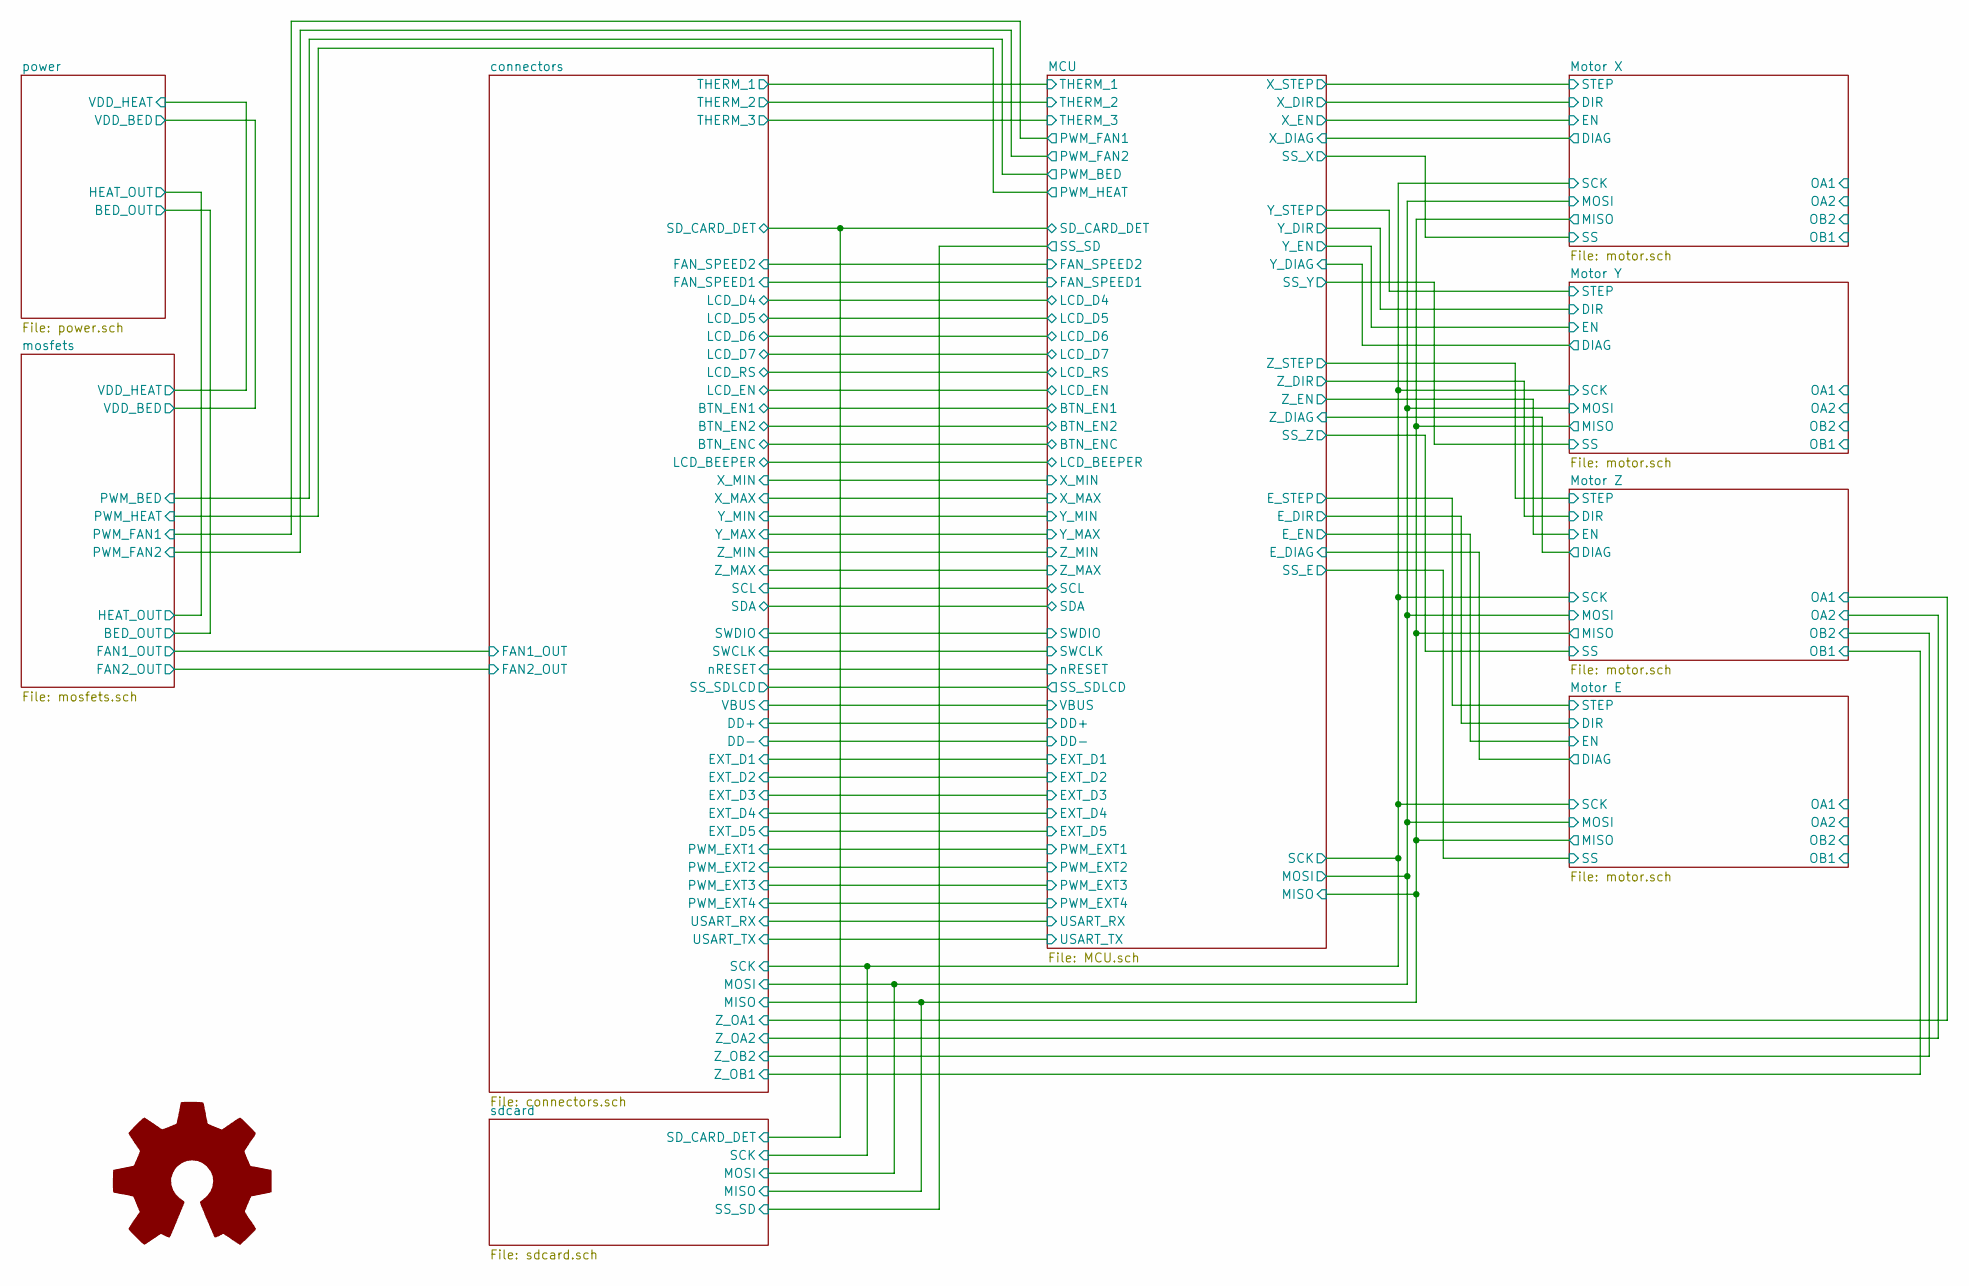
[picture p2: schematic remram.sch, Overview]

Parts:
LOGO1: Logo_Open_Hardware_Large; OSHW-Logo2_14.6x12mm_SilkScreen

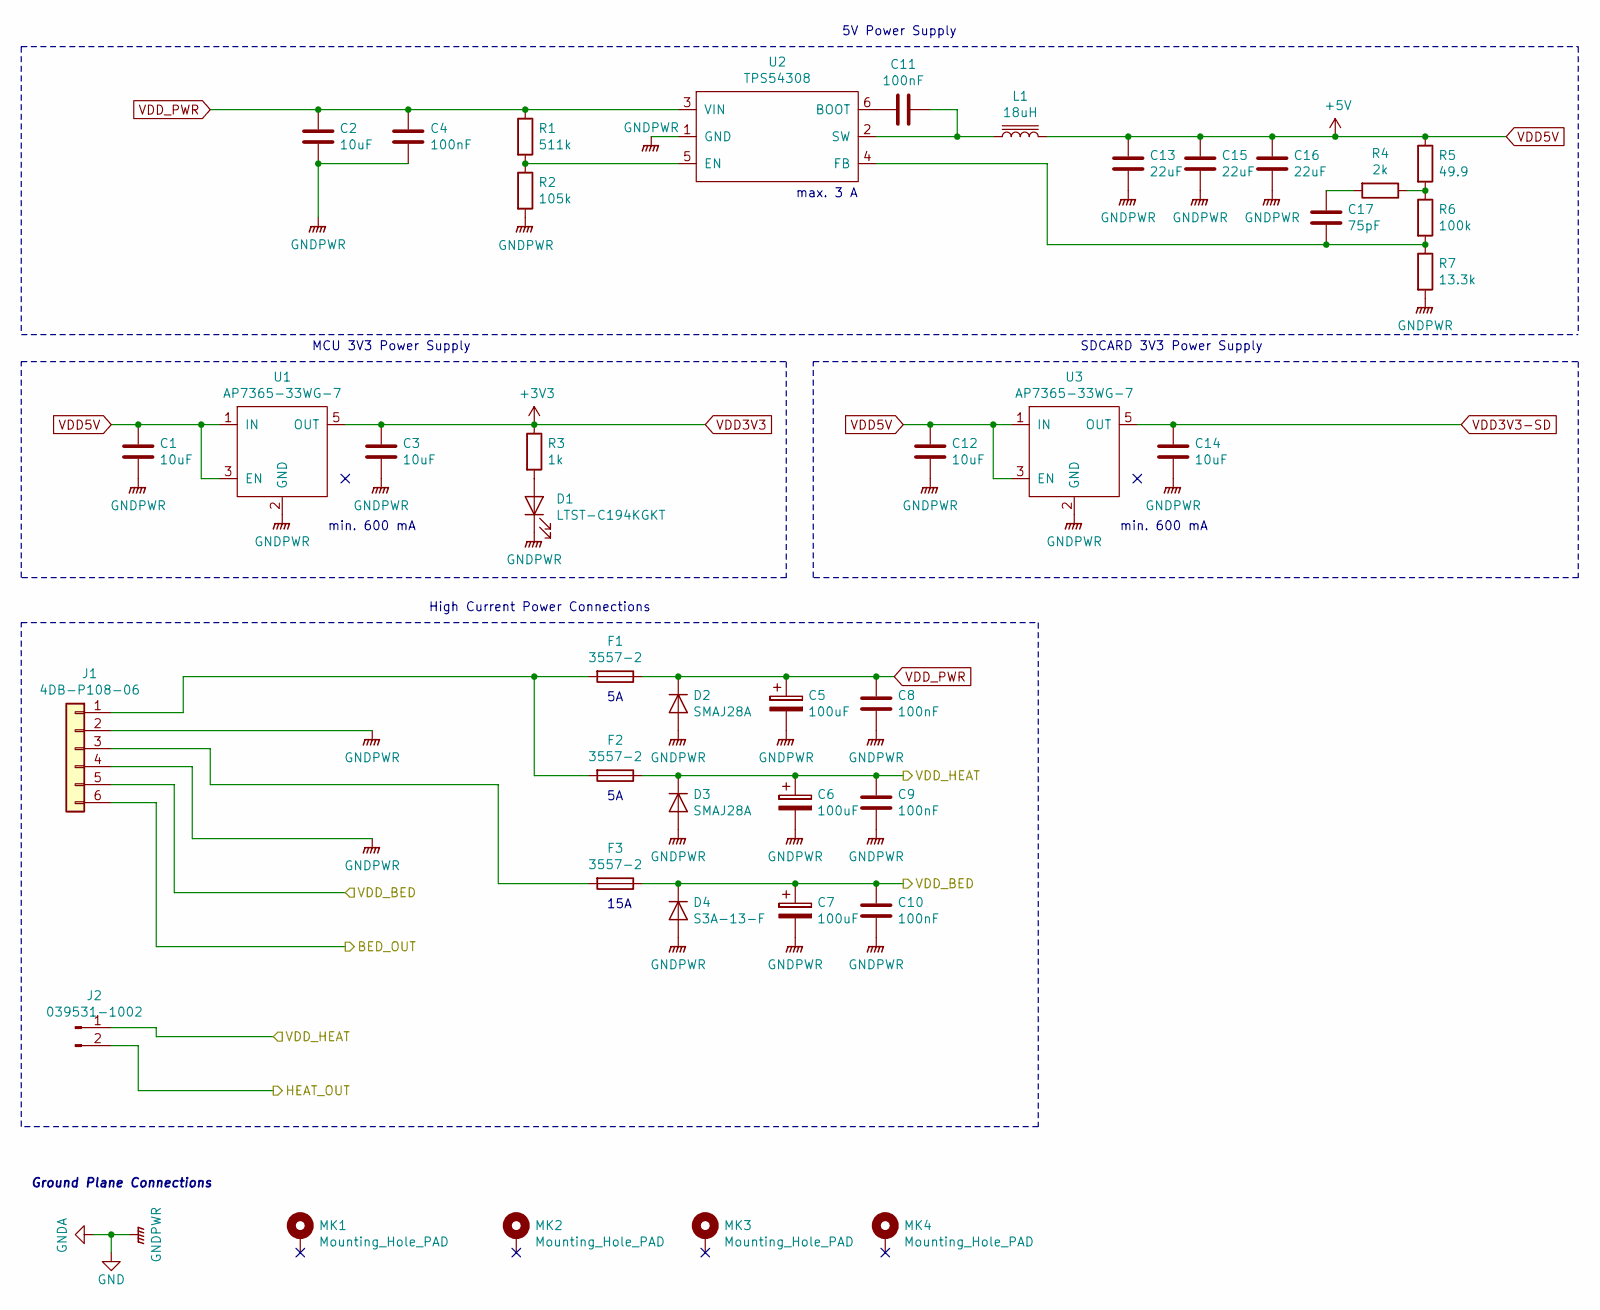
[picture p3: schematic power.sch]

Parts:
C1, C3, C12, C14: 10uF; C_0603_1608Metric
C2: 10uF; C_1206_3216Metric
C4: 100nF; C_1206_3216Metric
C5, C6, C7: 100uF; CP_Radial_D6.3mm_P2.50mm
C8, C9, C10: 100nF; C_1812_4532Metric
C11: 100nF; C_0603_1608Metric
C13, C15, C16: 22uF; C_1206_3216Metric
C17: 75pF; C_0603_1608Metric
D1: LTST-C194KGKT; LED_0603_1608Metric
D2, D3: SMAJ28A; D_SMA
D4: S3A-13-F; D_SMC
F1, F2, F3: 3557-2; KEYSTONE-FUSE-3557-2
J1: 4DB-P108-06
J2: 039531-1002; 39531-1002
L1: 18uH; L_Wuerth_WE-PDF
MK1, MK2, MK3, MK4: Mounting_Hole_PAD; MountingHole_3.5mm_Pad
R1: 511k; R_0603_1608Metric
R2: 105k; R_0603_1608Metric
R3: 1k; R_0603_1608Metric
R4: 2k; R_0603_1608Metric
R5: 49.9; R_0603_1608Metric
R6: 100k; R_0603_1608Metric
R7: 13.3k; R_0603_1608Metric
U1, U3: AP7365-33WG-7; SOT-23-5
U2: TPS54308; SOT-23-6

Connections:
/mosfets/BED_OUT: J1.6; also elsewhere on the board
/mosfets/HEAT_OUT: J2.2; also elsewhere on the board
/mosfets/VDD_BED: C7.1, C10.1, D4.1 (K), F3.1, J1.5; also elsewhere on the board
/mosfets/VDD_HEAT: C6.1, C9.1, D3.1 (K), F2.1, J2.1; also elsewhere on the board
GND: C1.2, C2.2, C3.2, C4.2, C5.2, C6.2, C7.2, C8.2, C9.2, C10.2, C12.2, C13.2, C14.2, C15.2, C16.2, D1.1 (K), D2.2 (A), D3.2 (A), D4.2 (A), J1.2, J1.4, R2.2, R7.2, U1.2 (GND), U2.1 (GND), U3.2 (GND); also elsewhere on the board
unnamed: C11.1, U2.6 (BOOT)
unnamed: C11.2, L1.1, U2.2 (SW)
unnamed: C17.1, R4.2
unnamed: C17.2, R6.2, R7.1, U2.4 (FB)
unnamed: D1.2 (A), R3.2
unnamed: F1.2, F2.2, J1.1
unnamed: F3.2, J1.3
unnamed: R1.2, R2.1, U2.5 (EN)
unnamed: R4.1, R5.2, R6.1
VDD3V3: C3.1, R3.1, U1.5 (OUT); also elsewhere on the board
VDD3V3-SD: C14.1, U3.5 (OUT); also elsewhere on the board
VDD5V: C1.1, C12.1, C13.1, C15.1, C16.1, L1.2, R5.1, U1.1 (IN), U1.3 (EN), U3.1 (IN), U3.3 (EN); also elsewhere on the board
VDD_PWR: C2.1, C4.1, C5.1, C8.1, D2.1 (K), F1.1, R1.1, U2.3 (VIN); also elsewhere on the board

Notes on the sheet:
min. 600 mA
max. 3 A
15A
Ground Plane Connections
High Current Power Connections
5V Power Supply
MCU 3V3 Power Supply
SDCARD 3V3 Power Supply

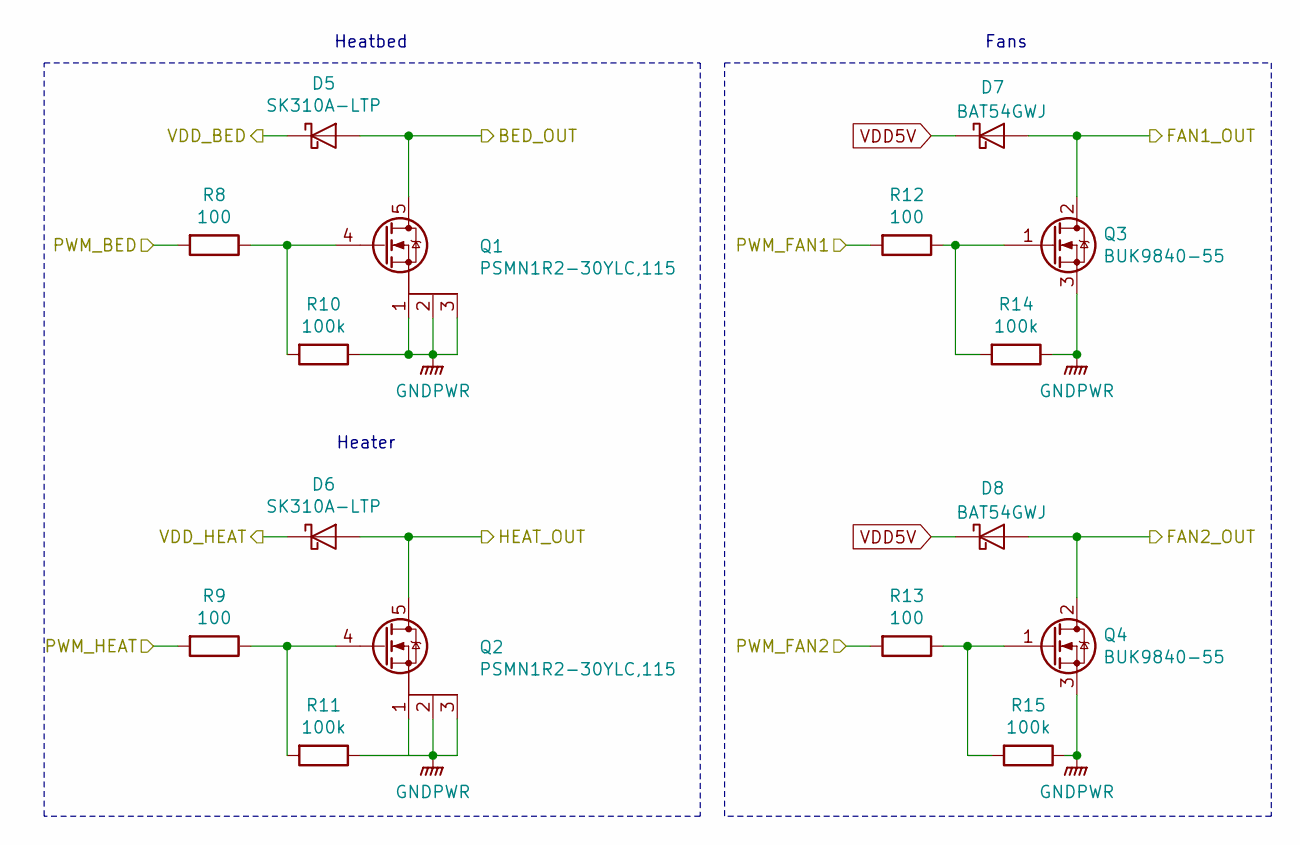
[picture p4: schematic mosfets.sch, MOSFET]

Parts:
D5, D6: SK310A-LTP; D_SMA
D7, D8: BAT54GWJ; D_SOD-123
Q1, Q2: PSMN1R2-30YLC,115; SOT-669_LFPAK_ThermalVias-1
Q3, Q4: BUK9840-55; SOT-223-3_TabPin2
R8, R9, R12, R13: 100; R_0603_1608Metric
R10, R11, R14, R15: 100k; R_0603_1608Metric

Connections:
/MCU/PWM_BED: R8.2; also elsewhere on the board
/MCU/PWM_FAN1: R12.2; also elsewhere on the board
/MCU/PWM_FAN2: R13.2; also elsewhere on the board
/MCU/PWM_HEAT: R9.2; also elsewhere on the board
/connectors/FAN1_OUT: D7.2 (A), Q3.2 (D); also elsewhere on the board
/connectors/FAN2_OUT: D8.2 (A), Q4.2 (D); also elsewhere on the board
/mosfets/BED_OUT: D5.2 (A), Q1.5 (D); also elsewhere on the board
/mosfets/HEAT_OUT: D6.2 (A), Q2.5 (D); also elsewhere on the board
/mosfets/VDD_BED: D5.1 (K); also elsewhere on the board
/mosfets/VDD_HEAT: D6.1 (K); also elsewhere on the board
GND: Q1.1 (S), Q1.2 (S), Q1.3 (S), Q2.1 (S), Q2.2 (S), Q2.3 (S), Q3.3 (S), Q4.3 (S), R10.1, R11.1, R14.1, R15.1; also elsewhere on the board
unnamed: Q1.4 (G), R8.1, R10.2
unnamed: Q2.4 (G), R9.1, R11.2
unnamed: Q3.1 (G), R12.1, R14.2
unnamed: Q4.1 (G), R13.1, R15.2
VDD5V: D7.1 (K), D8.1 (K); also elsewhere on the board

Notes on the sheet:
Heater
Heatbed
Fans

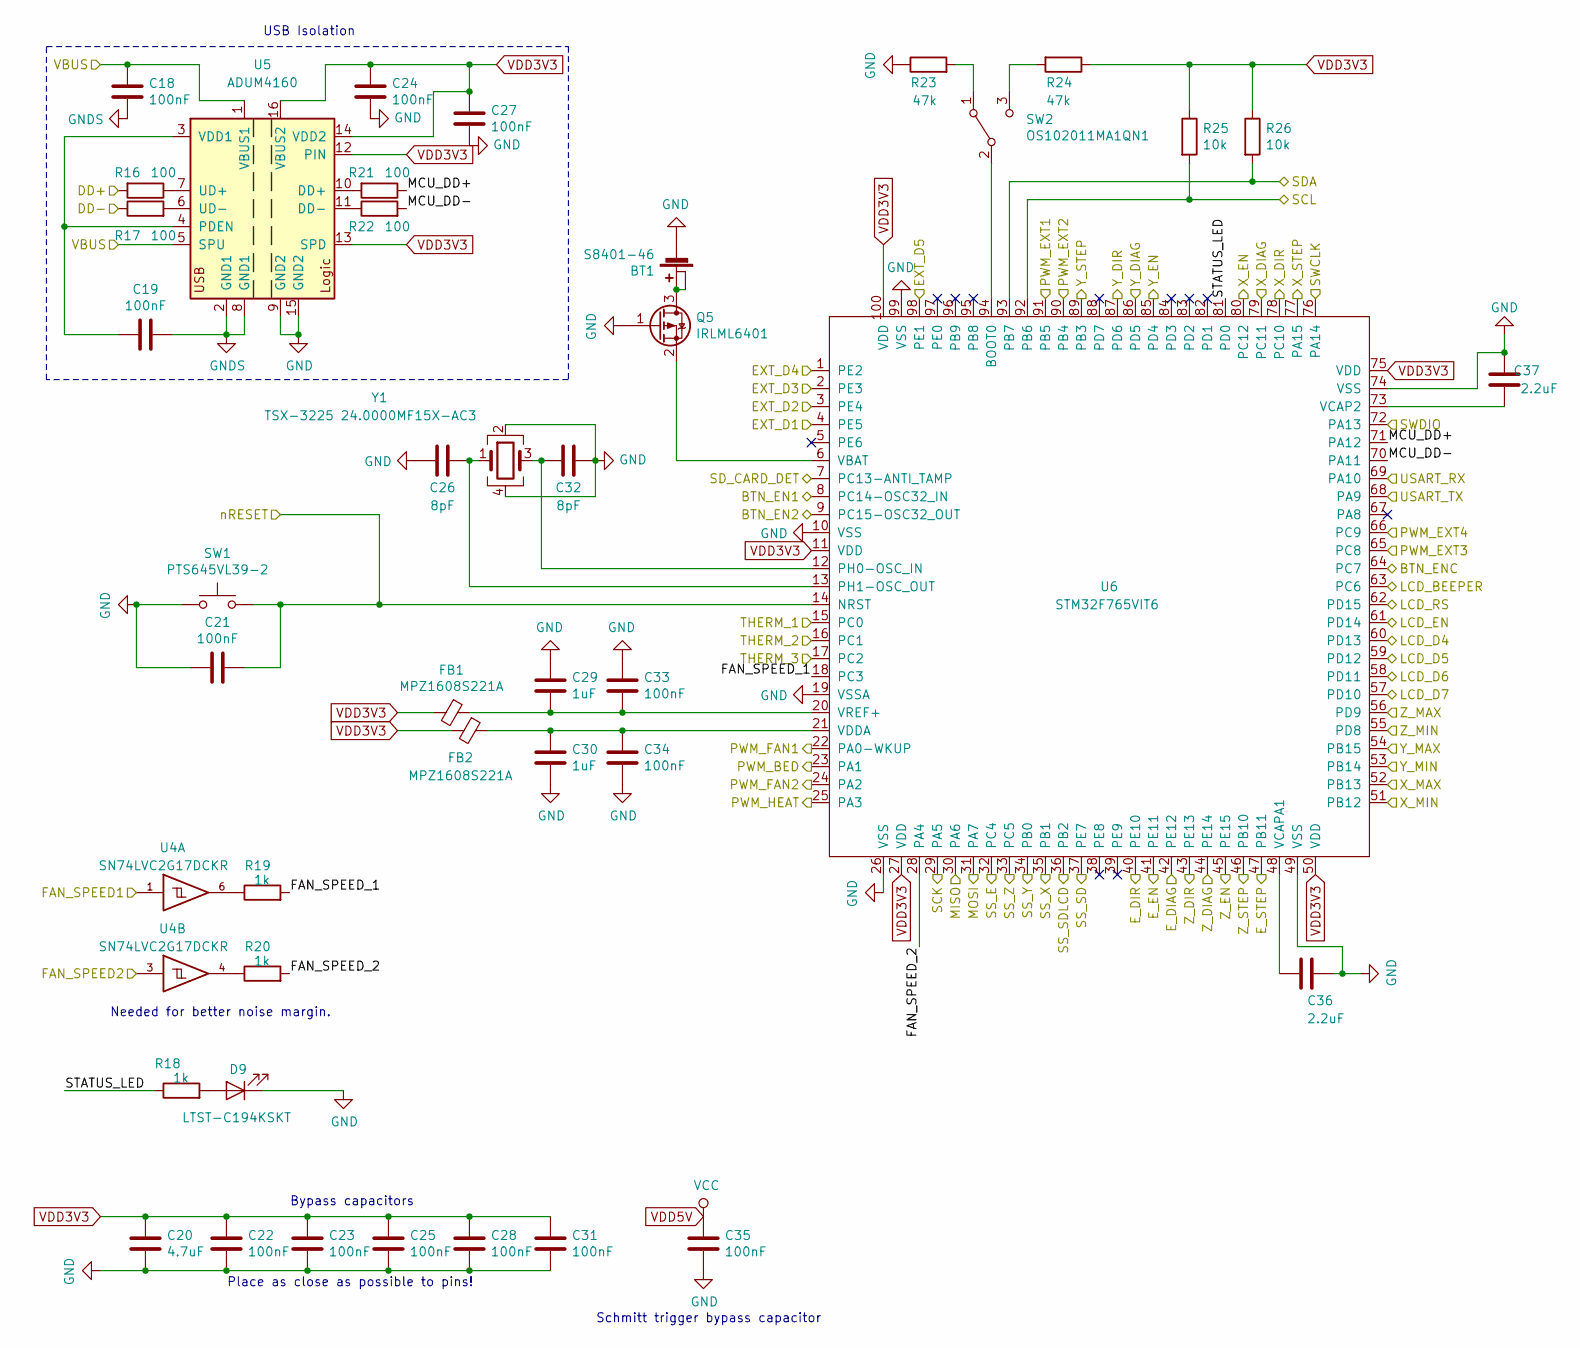
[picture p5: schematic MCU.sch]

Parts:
BT1: S8401-46
C18, C19, C21, C22, C23, C24, C25, C27, C28, C31, C33, C34, C35: 100nF; C_0603_1608Metric
C20: 4.7uF; C_0603_1608Metric
C26, C32: 8pF; C_0603_1608Metric
C29, C30: 1uF; C_0603_1608Metric
C36, C37: 2.2uF; C_0603_1608Metric
D9: LTST-C194KSKT; LED_0603_1608Metric
FB1, FB2: MPZ1608S221A; R_0603_1608Metric
Q5: IRLML6401; SOT-23
R16, R17, R21, R22: 100; R_0603_1608Metric
R18, R19, R20: 1k; R_0603_1608Metric
R23, R24: 47k; R_0603_1608Metric
R25, R26: 10k; R_0603_1608Metric
SW1: PTS645VL39-2; SW_Tactile_SPST_Angled_PTS645Vx39-2LFS
SW2: OS102011MA1QN1; SW_CuK_OS102011MA1QN1_SPDT_Angled
U4: SN74LVC2G17DCKR; SOT-363_SC-70-6
U5: ADUM4160; SOIC-16W_7.5x10.3mm_P1.27mm
U6: STM32F765VIT6; TQFP-100_14x14mm_P0.5mm
Y1: TSX-3225 24.0000MF15X-AC3; Crystal_SMD_SeikoEpson_TSX3225-4Pin_3.2x2.5mm

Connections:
/MCU/BTN_EN1: U6.8 (PC14-OSC32_IN); also elsewhere on the board
/MCU/BTN_EN2: U6.9 (PC15-OSC32_OUT); also elsewhere on the board
/MCU/BTN_ENC: U6.64 (PC7); also elsewhere on the board
/MCU/DD+: R16.2; also elsewhere on the board
/MCU/DD-: R17.1; also elsewhere on the board
/MCU/EXT_D1: U6.4 (PE5); also elsewhere on the board
/MCU/EXT_D2: U6.3 (PE4); also elsewhere on the board
/MCU/EXT_D3: U6.2 (PE3); also elsewhere on the board
/MCU/EXT_D4: U6.1 (PE2); also elsewhere on the board
/MCU/EXT_D5: U6.98 (PE1); also elsewhere on the board
/MCU/E_STEP: U6.47 (PB11); also elsewhere on the board
/MCU/FAN_SPEED1: U4.1; also elsewhere on the board
/MCU/FAN_SPEED2: U4.3; also elsewhere on the board
/MCU/FAN_SPEED_1: R19.2, U6.18 (PC3)
/MCU/FAN_SPEED_2: R20.2, U6.28 (PA4)
/MCU/LCD_BEEPER: U6.63 (PC6); also elsewhere on the board
/MCU/LCD_D4: U6.60 (PD13); also elsewhere on the board
/MCU/LCD_D5: U6.59 (PD12); also elsewhere on the board
/MCU/LCD_D6: U6.58 (PD11); also elsewhere on the board
/MCU/LCD_D7: U6.57 (PD10); also elsewhere on the board
/MCU/LCD_EN: U6.61 (PD14); also elsewhere on the board
/MCU/LCD_RS: U6.62 (PD15); also elsewhere on the board
/MCU/MCU_DD+: R21.1, U6.71 (PA12)
/MCU/MCU_DD-: R22.2, U6.70 (PA11)
/MCU/MISO: U6.30 (PA6); also elsewhere on the board
/MCU/MOSI: U6.31 (PA7); also elsewhere on the board
/MCU/PWM_BED: U6.23 (PA1); also elsewhere on the board
/MCU/PWM_EXT1: U6.91 (PB5); also elsewhere on the board
/MCU/PWM_EXT2: U6.90 (PB4); also elsewhere on the board
/MCU/PWM_EXT3: U6.65 (PC8); also elsewhere on the board
/MCU/PWM_EXT4: U6.66 (PC9); also elsewhere on the board
/MCU/PWM_FAN1: U6.22 (PA0-WKUP); also elsewhere on the board
/MCU/PWM_FAN2: U6.24 (PA2); also elsewhere on the board
/MCU/PWM_HEAT: U6.25 (PA3); also elsewhere on the board
/MCU/SCK: U6.29 (PA5); also elsewhere on the board
/MCU/SCL: R25.2, U6.92 (PB6); also elsewhere on the board
/MCU/SDA: R26.2, U6.93 (PB7); also elsewhere on the board
/MCU/SD_CARD_DET: U6.7 (PC13-ANTI_TAMP); also elsewhere on the board
/MCU/SS_SD: U6.37 (PE7); also elsewhere on the board
/MCU/SS_SDLCD: U6.36 (PB2); also elsewhere on the board
/MCU/STATUS_LED: R18.1, U6.81 (PD0)
/MCU/SWCLK: U6.76 (PA14); also elsewhere on the board
/MCU/SWDIO: U6.72 (PA13); also elsewhere on the board
/MCU/THERM_1: U6.15 (PC0); also elsewhere on the board
/MCU/THERM_2: U6.16 (PC1); also elsewhere on the board
/MCU/THERM_3: U6.17 (PC2); also elsewhere on the board
/MCU/USART_RX: U6.69 (PA10); also elsewhere on the board
/MCU/USART_TX: U6.68 (PA9); also elsewhere on the board
/MCU/VBUS: C18.1, U5.1 (VBUS1), U5.5 (SPU); also elsewhere on the board
/MCU/X_MAX: U6.52 (PB13); also elsewhere on the board
/MCU/X_MIN: U6.51 (PB12); also elsewhere on the board
/MCU/Y_MAX: U6.54 (PB15); also elsewhere on the board
/MCU/Y_MIN: U6.53 (PB14); also elsewhere on the board
/MCU/Z_MAX: U6.56 (PD9); also elsewhere on the board
/MCU/Z_MIN: U6.55 (PD8); also elsewhere on the board
/MCU/nRESET: C21.2, SW1.2, U6.14 (NRST); also elsewhere on the board
/Motor E/DIAG: U6.42 (PE12); also elsewhere on the board
/Motor E/DIR: U6.40 (PE10); also elsewhere on the board
/Motor E/EN: U6.41 (PE11); also elsewhere on the board
/Motor E/SS: U6.32 (PC4); also elsewhere on the board
/Motor X/DIAG: U6.79 (PC11); also elsewhere on the board
/Motor X/DIR: U6.78 (PC10); also elsewhere on the board
/Motor X/EN: U6.80 (PC12); also elsewhere on the board
/Motor X/SS: U6.35 (PB1); also elsewhere on the board
/Motor X/STEP: U6.77 (PA15); also elsewhere on the board
/Motor Y/DIAG: U6.86 (PD5); also elsewhere on the board
/Motor Y/DIR: U6.87 (PD6); also elsewhere on the board
/Motor Y/EN: U6.85 (PD4); also elsewhere on the board
/Motor Y/SS: U6.34 (PB0); also elsewhere on the board
/Motor Y/STEP: U6.89 (PB3); also elsewhere on the board
/Motor Z/DIAG: U6.44 (PE14); also elsewhere on the board
/Motor Z/DIR: U6.43 (PE13); also elsewhere on the board
/Motor Z/EN: U6.45 (PE15); also elsewhere on the board
/Motor Z/SS: U6.33 (PC5); also elsewhere on the board
/Motor Z/STEP: U6.46 (PB10); also elsewhere on the board
GND: BT1.1 (-), C20.2, C21.1, C22.2, C23.2, C24.2, C25.2, C26.1, C27.1, C28.2, C29.1, C30.2, C31.2, C32.2, C33.1, C34.2, C35.2, C36.1, C37.2, D9.1 (K), Q5.1 (G), R23.1, SW1.1, U4.2 (GND), U5.9 (GND2), U5.15 (GND2), U6.10 (VSS), U6.19 (VSSA), U6.26 (VSS), U6.49 (VSS), U6.74 (VSS), U6.99 (VSS), Y1.2, Y1.4; also elsewhere on the board
GNDS: C18.2, C19.1, U5.2 (GND1), U5.8 (GND1); also elsewhere on the board
unnamed: BT1.2 (+), BT1.3 (+), Q5.3 (D)
unnamed: C19.2, U5.3 (VDD1), U5.4 (PDEN)
unnamed: C26.2, U6.13 (PH1-OSC_OUT), Y1.1
unnamed: C29.2, C33.2, FB1.1, U6.20 (VREF+)
unnamed: C30.1, C34.1, FB2.1, U6.21 (VDDA)
unnamed: C32.1, U6.12 (PH0-OSC_IN), Y1.3
unnamed: C36.2, U6.48 (VCAPA1)
unnamed: C37.1, U6.73 (VCAP2)
unnamed: D9.2 (A), R18.2
unnamed: Q5.2 (S), U6.6 (VBAT)
unnamed: R16.1, U5.7 (UD+)
unnamed: R17.2, U5.6 (UD-)
unnamed: R19.1, U4.6
unnamed: R20.1, U4.4
unnamed: R21.2, U5.10 (DD+)
unnamed: R22.1, U5.11 (DD-)
unnamed: R23.2, SW2.1 (A)
unnamed: R24.2, SW2.3 (C)
unnamed: SW2.2 (B), U6.94 (BOOT0)
VDD3V3: C20.1, C22.1, C23.1, C24.1, C25.1, C27.2, C28.1, C31.1, FB1.2, FB2.2, R24.1, R25.1, R26.1, U5.12 (PIN), U5.13 (SPD), U5.14 (VDD2), U5.16 (VBUS2), U6.11 (VDD), U6.27 (VDD), U6.50 (VDD), U6.75 (VDD), U6.100 (VDD); also elsewhere on the board
VDD5V: C35.1, U4.5 (VCC); also elsewhere on the board

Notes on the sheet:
Place as close as possible to pins!
Bypass capacitors
USB Isolation
Needed for better noise margin.
Schmitt trigger bypass capacitor

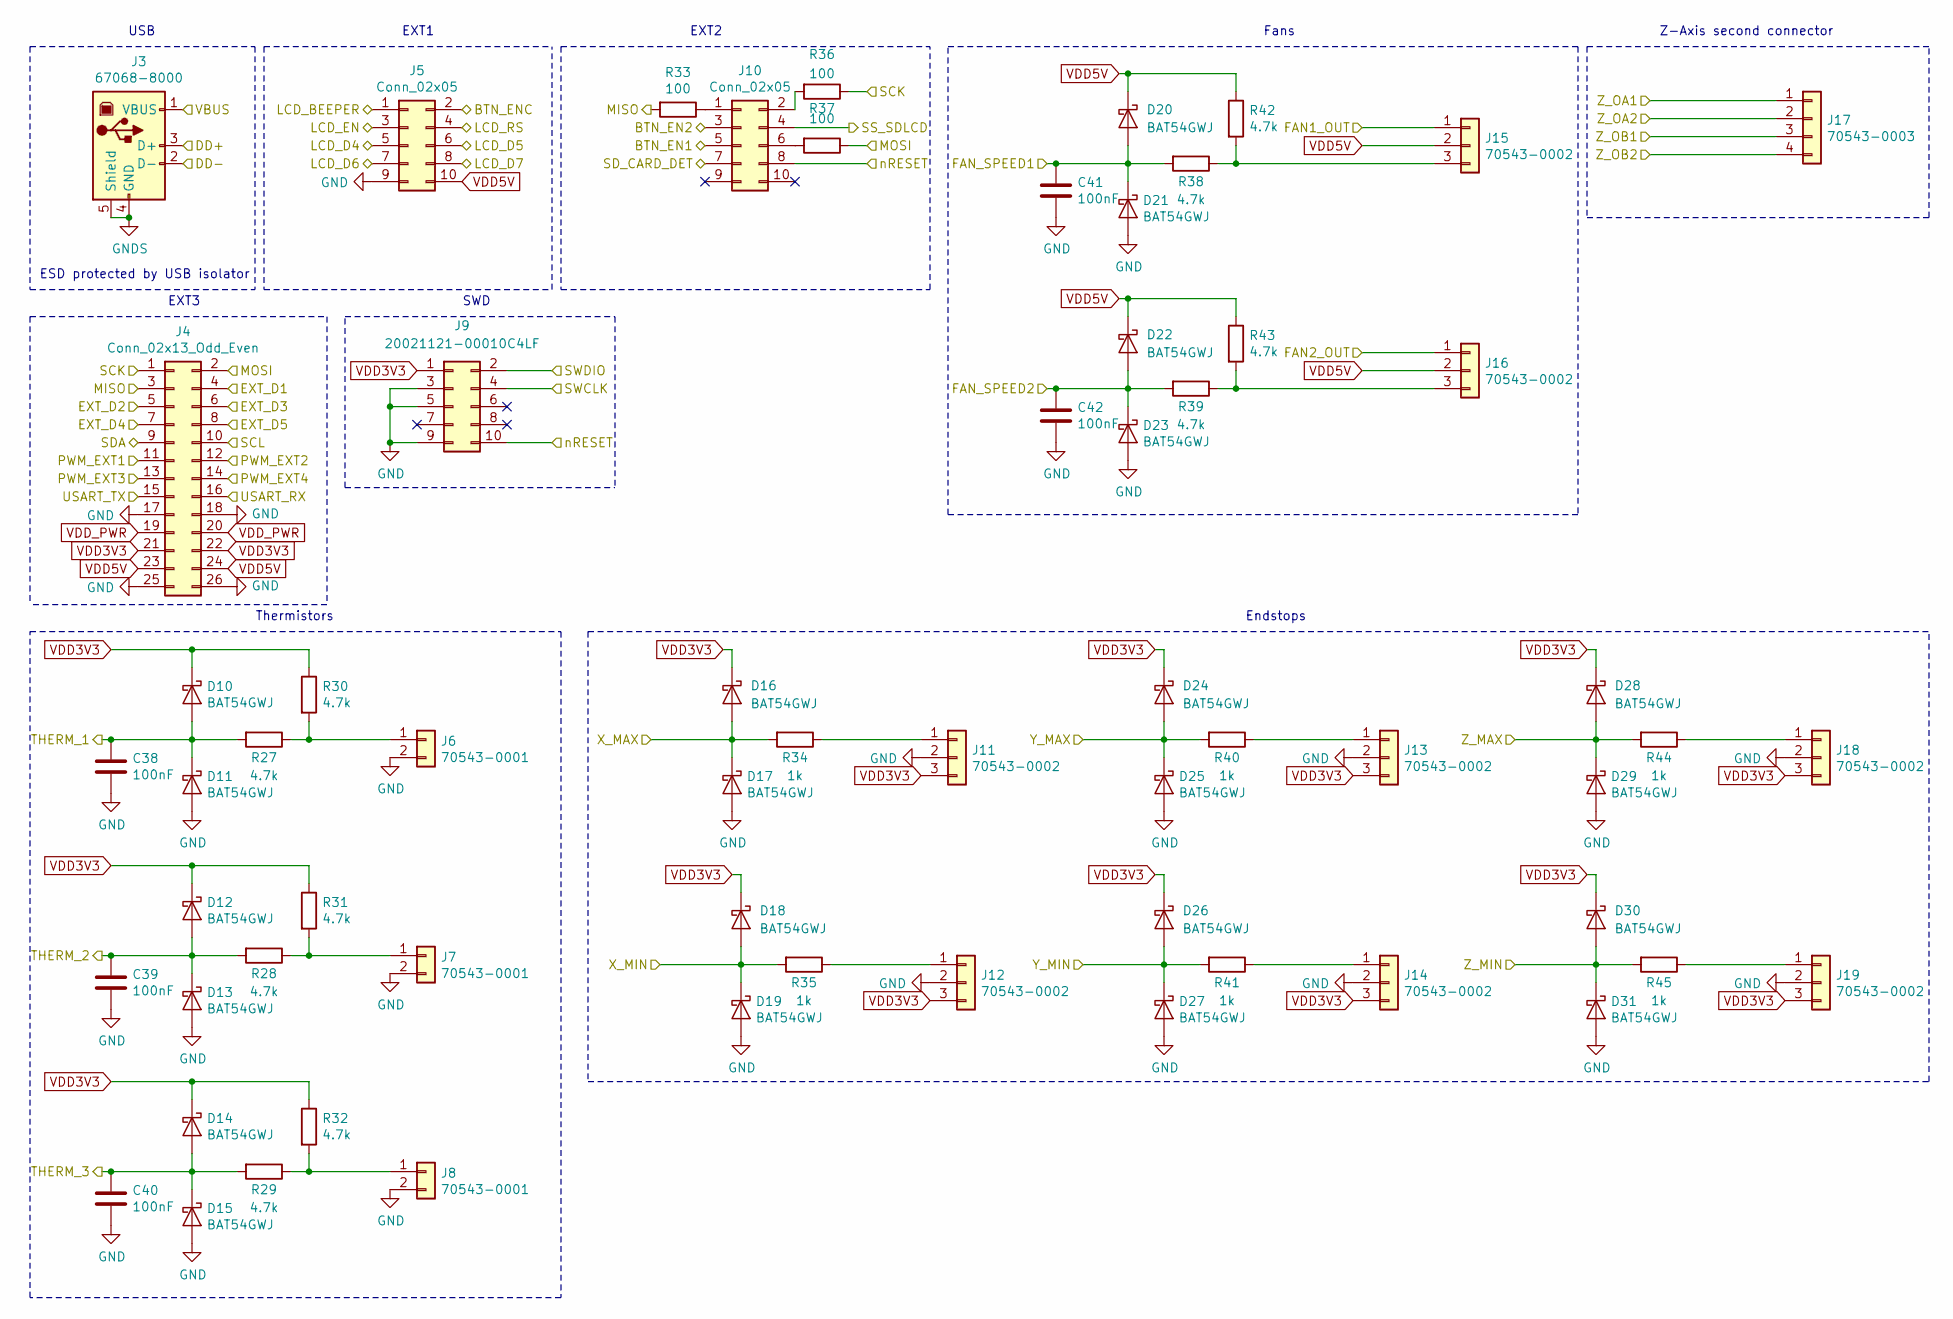
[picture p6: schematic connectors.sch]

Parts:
C38, C39, C40, C41, C42: 100nF; C_0603_1608Metric
D10, D11, D12, D13, D14, D15, D16, D17, D18, D19, D20, D21, D22, D23, D24, D25, D26, D27, D28, D29, D30, D31: BAT54GWJ; D_SOD-123
J3: 67068-8000
J4: Conn_02x13_Odd_Even; PinHeader_2x13_P2.54mm_Vertical
J5, J10: Conn_02x05; PinHeader_2x05_P2.54mm_Vertical
J6, J7, J8: 70543-0001
J9: 20021121-00010C4LF; PinHeader_2x05_P1.27mm_Vertical_SMD
J11, J12, J13, J14, J15, J16, J18, J19: 70543-0002
J17: 70543-0003
R27, R28, R29, R30, R31, R32, R38, R39, R42, R43: 4.7k; R_0603_1608Metric
R33, R36, R37: 100; R_0603_1608Metric
R34, R35, R40, R41, R44, R45: 1k; R_0603_1608Metric

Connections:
/MCU/BTN_EN1: J10.5; also elsewhere on the board
/MCU/BTN_EN2: J10.3; also elsewhere on the board
/MCU/BTN_ENC: J5.2; also elsewhere on the board
/MCU/DD+: J3.3 (D+); also elsewhere on the board
/MCU/DD-: J3.2 (D-); also elsewhere on the board
/MCU/EXT_D1: J4.4; also elsewhere on the board
/MCU/EXT_D2: J4.5; also elsewhere on the board
/MCU/EXT_D3: J4.6; also elsewhere on the board
/MCU/EXT_D4: J4.7; also elsewhere on the board
/MCU/EXT_D5: J4.8; also elsewhere on the board
/MCU/FAN_SPEED1: C41.1, D20.2 (A), D21.1 (K), R38.2; also elsewhere on the board
/MCU/FAN_SPEED2: C42.1, D22.2 (A), D23.1 (K), R39.2; also elsewhere on the board
/MCU/LCD_BEEPER: J5.1; also elsewhere on the board
/MCU/LCD_D4: J5.5; also elsewhere on the board
/MCU/LCD_D5: J5.6; also elsewhere on the board
/MCU/LCD_D6: J5.7; also elsewhere on the board
/MCU/LCD_D7: J5.8; also elsewhere on the board
/MCU/LCD_EN: J5.3; also elsewhere on the board
/MCU/LCD_RS: J5.4; also elsewhere on the board
/MCU/MISO: J4.3, R33.2; also elsewhere on the board
/MCU/MOSI: J4.2, R37.1; also elsewhere on the board
/MCU/PWM_EXT1: J4.11; also elsewhere on the board
/MCU/PWM_EXT2: J4.12; also elsewhere on the board
/MCU/PWM_EXT3: J4.13; also elsewhere on the board
/MCU/PWM_EXT4: J4.14; also elsewhere on the board
/MCU/SCK: J4.1, R36.1; also elsewhere on the board
/MCU/SCL: J4.10; also elsewhere on the board
/MCU/SDA: J4.9; also elsewhere on the board
/MCU/SD_CARD_DET: J10.7; also elsewhere on the board
/MCU/SS_SDLCD: J10.4; also elsewhere on the board
/MCU/SWCLK: J9.4; also elsewhere on the board
/MCU/SWDIO: J9.2; also elsewhere on the board
/MCU/THERM_1: C38.1, D10.2 (A), D11.1 (K), R27.2; also elsewhere on the board
/MCU/THERM_2: C39.1, D12.2 (A), D13.1 (K), R28.2; also elsewhere on the board
/MCU/THERM_3: C40.1, D14.2 (A), D15.1 (K), R29.2; also elsewhere on the board
/MCU/USART_RX: J4.16; also elsewhere on the board
/MCU/USART_TX: J4.15; also elsewhere on the board
/MCU/VBUS: J3.1 (VBUS); also elsewhere on the board
/MCU/X_MAX: D16.2 (A), D17.1 (K), R34.2; also elsewhere on the board
/MCU/X_MIN: D18.2 (A), D19.1 (K), R35.2; also elsewhere on the board
/MCU/Y_MAX: D24.2 (A), D25.1 (K), R40.2; also elsewhere on the board
/MCU/Y_MIN: D26.2 (A), D27.1 (K), R41.2; also elsewhere on the board
/MCU/Z_MAX: D28.2 (A), D29.1 (K), R44.2; also elsewhere on the board
/MCU/Z_MIN: D30.2 (A), D31.1 (K), R45.2; also elsewhere on the board
/MCU/nRESET: J9.10, J10.8; also elsewhere on the board
/Motor Z/OA1: J17.1; also elsewhere on the board
/Motor Z/OA2: J17.2; also elsewhere on the board
/Motor Z/OB1: J17.3; also elsewhere on the board
/Motor Z/OB2: J17.4; also elsewhere on the board
/connectors/FAN1_OUT: J15.1; also elsewhere on the board
/connectors/FAN2_OUT: J16.1; also elsewhere on the board
GND: C38.2, C39.2, C40.2, C41.2, C42.2, D11.2 (A), D13.2 (A), D15.2 (A), D17.2 (A), D19.2 (A), D21.2 (A), D23.2 (A), D25.2 (A), D27.2 (A), D29.2 (A), D31.2 (A), J4.17, J4.18, J4.25, J4.26, J5.9, J6.2, J7.2, J8.2, J9.3, J9.5, J9.9, J11.2, J12.2, J13.2, J14.2, J18.2, J19.2; also elsewhere on the board
GNDS: J3.4 (GND), J3.5 (Shield); also elsewhere on the board
unnamed: J6.1, R27.1, R30.2
unnamed: J7.1, R28.1, R31.2
unnamed: J8.1, R29.1, R32.2
unnamed: J10.1, R33.1
unnamed: J10.2, R36.2
unnamed: J10.6, R37.2
unnamed: J11.1, R34.1
unnamed: J12.1, R35.1
unnamed: J13.1, R40.1
unnamed: J14.1, R41.1
unnamed: J15.3, R38.1, R42.2
unnamed: J16.3, R39.1, R43.2
unnamed: J18.1, R44.1
unnamed: J19.1, R45.1
VDD3V3: D10.1 (K), D12.1 (K), D14.1 (K), D16.1 (K), D18.1 (K), D24.1 (K), D26.1 (K), D28.1 (K), D30.1 (K), J4.21, J4.22, J9.1, J11.3, J12.3, J13.3, J14.3, J18.3, J19.3, R30.1, R31.1, R32.1; also elsewhere on the board
VDD5V: D20.1 (K), D22.1 (K), J4.23, J4.24, J5.10, J15.2, J16.2, R42.1, R43.1; also elsewhere on the board
VDD_PWR: J4.19, J4.20; also elsewhere on the board

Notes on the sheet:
USB
EXT1
EXT2
EXT3
Thermistors
Endstops
SWD
ESD protected by USB isolator
Fans
Z-Axis second connector

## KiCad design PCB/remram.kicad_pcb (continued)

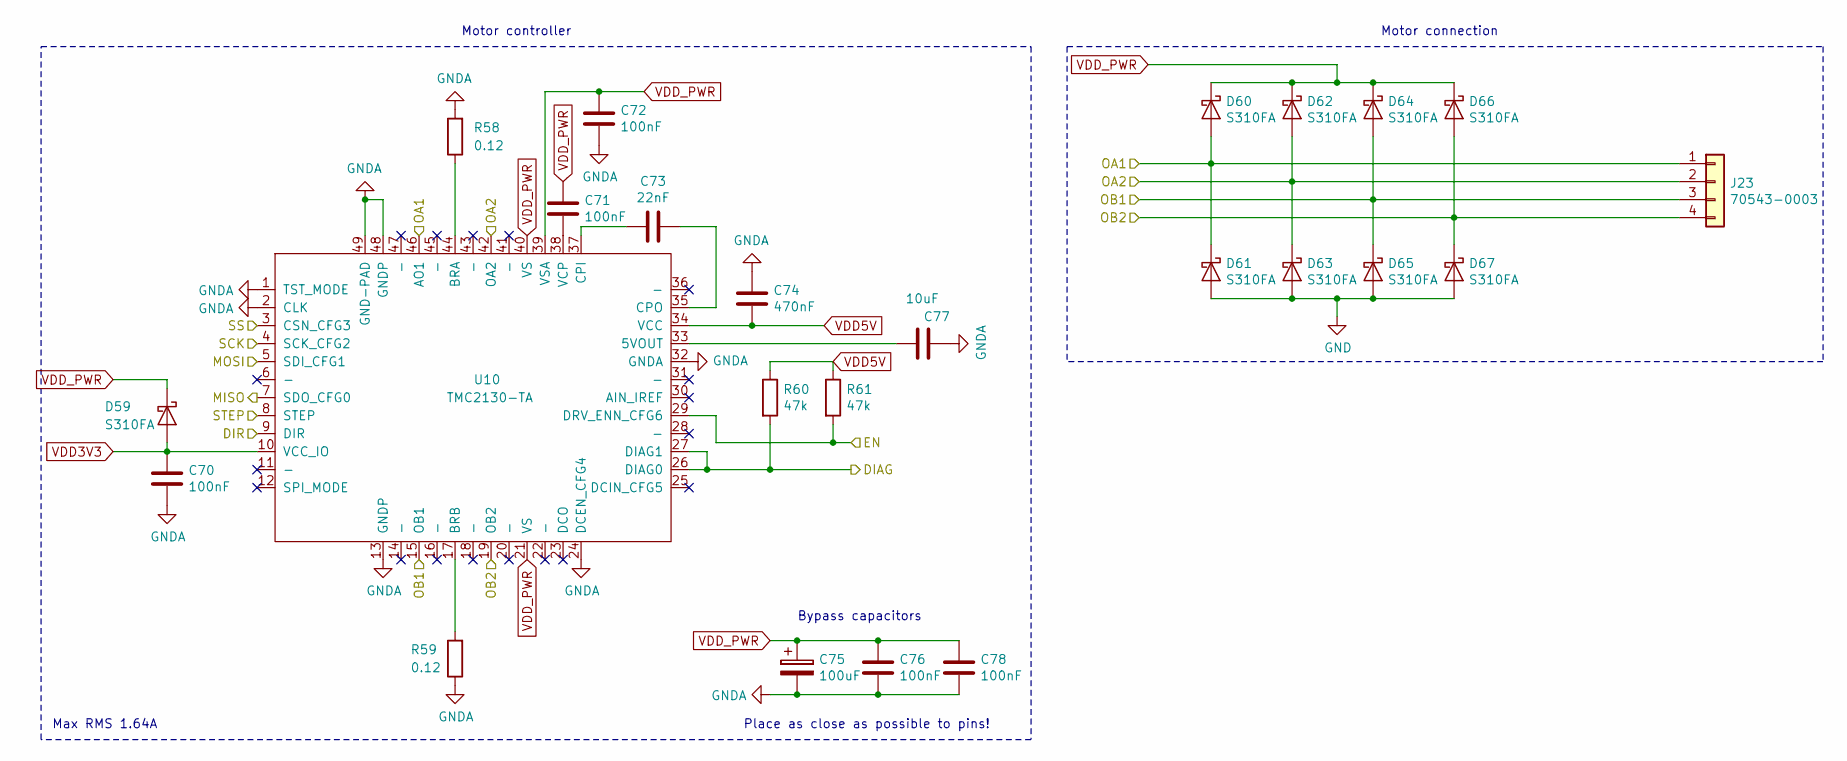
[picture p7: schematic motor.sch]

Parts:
C43, C44, C45, C49, C51: 100nF; C_0603_1608Metric
C46: 22nF; C_0603_1608Metric
C47: 470nF; C_0603_1608Metric
C48: 100uF; CP_Radial_D6.3mm_P2.50mm
C50: 10uF; C_0603_1608Metric
D32, D33, D34, D35, D36, D37, D38, D39, D40: S310FA; D_SOD-123
J20: 70543-0003
R46, R47: 0.12; R_1206_3216Metric
R48, R49: 47k; R_0603_1608Metric
U7: TMC2130-TA; TQFP-48-1EP_7x7mm_P0.5mm_EP4.8x4.8mm-Heatsink

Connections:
/MCU/MISO: U7.7 (SDO_CFG0); also elsewhere on the board
/MCU/MOSI: U7.5 (SDI_CFG1); also elsewhere on the board
/MCU/SCK: U7.4 (SCK_CFG2); also elsewhere on the board
/Motor X/DIAG: R48.2, U7.26 (DIAG0), U7.27 (DIAG1); also elsewhere on the board
/Motor X/DIR: U7.9 (DIR); also elsewhere on the board
/Motor X/EN: R49.2, U7.29 (DRV_ENN_CFG6); also elsewhere on the board
/Motor X/OA1: D33.2 (A), D34.1 (K), J20.1, U7.46 (AO1)
/Motor X/OA2: D35.2 (A), D36.1 (K), J20.2, U7.42 (OA2)
/Motor X/OB1: D37.2 (A), D38.1 (K), J20.3, U7.15 (OB1)
/Motor X/OB2: D39.2 (A), D40.1 (K), J20.4, U7.19 (OB2)
/Motor X/SS: U7.3 (CSN_CFG3); also elsewhere on the board
/Motor X/STEP: U7.8 (STEP); also elsewhere on the board
GND: C43.2, C45.2, C47.2, C48.2, C49.2, C50.2, C51.2, D34.2 (A), D36.2 (A), D38.2 (A), D40.2 (A), R46.2, R47.1, U7.1 (TST_MODE), U7.2 (CLK), U7.13 (GNDP), U7.24 (DCEN_CFG4), U7.32 (GNDA), U7.48 (GNDP), U7.49 (GND-PAD); also elsewhere on the board
unnamed: C44.2, U7.38 (VCP)
unnamed: C46.1, U7.35 (CPO)
unnamed: C46.2, U7.37 (CPI)
unnamed: C50.1, U7.33 (5VOUT)
unnamed: R46.1, U7.44 (BRA)
unnamed: R47.2, U7.17 (BRB)
VDD3V3: C43.1, D32.2 (A), U7.10 (VCC_IO); also elsewhere on the board
VDD5V: C47.1, R48.1, R49.1, U7.34 (VCC); also elsewhere on the board
VDD_PWR: C44.1, C45.1, C48.1, C49.1, C51.1, D32.1 (K), D33.1 (K), D35.1 (K), D37.1 (K), D39.1 (K), U7.21 (VS), U7.39 (VSA), U7.40 (VS); also elsewhere on the board

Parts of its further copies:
C52, C53, C54, C58, C60, C61, C62, C63, C67, C69, C70, C71, C72, C76, C78: 100nF; C_0603_1608Metric
C55, C64, C73: 22nF; C_0603_1608Metric
C56, C65, C74: 470nF; C_0603_1608Metric
C57, C66, C75: 100uF; CP_Radial_D6.3mm_P2.50mm
C59, C68, C77: 10uF; C_0603_1608Metric
D41, D42, D43, D44, D45, D46, D47, D48, D49, D50, D51, D52, D53, D54, D55, D56, D57, D58, D59, D60, D61, D62, D63, D64, D65, D66, D67: S310FA; D_SOD-123
J21, J22, J23: 70543-0003
R50, R51, R54, R55, R58, R59: 0.12; R_1206_3216Metric
R52, R53, R56, R57, R60, R61: 47k; R_0603_1608Metric
U8, U9, U10: TMC2130-TA; TQFP-48-1EP_7x7mm_P0.5mm_EP4.8x4.8mm-Heatsink

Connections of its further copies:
/MCU/E_STEP: U10.8 (STEP); also elsewhere on the board
/MCU/MISO: U8.7 (SDO_CFG0), U9.7 (SDO_CFG0), U10.7 (SDO_CFG0); also elsewhere on the board
/MCU/MOSI: U8.5 (SDI_CFG1), U9.5 (SDI_CFG1), U10.5 (SDI_CFG1); also elsewhere on the board
/MCU/SCK: U8.4 (SCK_CFG2), U9.4 (SCK_CFG2), U10.4 (SCK_CFG2); also elsewhere on the board
/Motor E/DIAG: R60.2, U10.26 (DIAG0), U10.27 (DIAG1); also elsewhere on the board
/Motor E/DIR: U10.9 (DIR); also elsewhere on the board
/Motor E/EN: R61.2, U10.29 (DRV_ENN_CFG6); also elsewhere on the board
/Motor E/OA1: D60.2 (A), D61.1 (K), J23.1, U10.46 (AO1)
/Motor E/OA2: D62.2 (A), D63.1 (K), J23.2, U10.42 (OA2)
/Motor E/OB1: D64.2 (A), D65.1 (K), J23.3, U10.15 (OB1)
/Motor E/OB2: D66.2 (A), D67.1 (K), J23.4, U10.19 (OB2)
/Motor E/SS: U10.3 (CSN_CFG3); also elsewhere on the board
/Motor Y/DIAG: R52.2, U8.26 (DIAG0), U8.27 (DIAG1); also elsewhere on the board
/Motor Y/DIR: U8.9 (DIR); also elsewhere on the board
/Motor Y/EN: R53.2, U8.29 (DRV_ENN_CFG6); also elsewhere on the board
/Motor Y/OA1: D42.2 (A), D43.1 (K), J21.1, U8.46 (AO1)
/Motor Y/OA2: D44.2 (A), D45.1 (K), J21.2, U8.42 (OA2)
/Motor Y/OB1: D46.2 (A), D47.1 (K), J21.3, U8.15 (OB1)
/Motor Y/OB2: D48.2 (A), D49.1 (K), J21.4, U8.19 (OB2)
/Motor Y/SS: U8.3 (CSN_CFG3); also elsewhere on the board
/Motor Y/STEP: U8.8 (STEP); also elsewhere on the board
/Motor Z/DIAG: R56.2, U9.26 (DIAG0), U9.27 (DIAG1); also elsewhere on the board
/Motor Z/DIR: U9.9 (DIR); also elsewhere on the board
/Motor Z/EN: R57.2, U9.29 (DRV_ENN_CFG6); also elsewhere on the board
/Motor Z/OA1: D51.2 (A), D52.1 (K), J22.1, U9.46 (AO1); also elsewhere on the board
/Motor Z/OA2: D53.2 (A), D54.1 (K), J22.2, U9.42 (OA2); also elsewhere on the board
/Motor Z/OB1: D55.2 (A), D56.1 (K), J22.3, U9.15 (OB1); also elsewhere on the board
/Motor Z/OB2: D57.2 (A), D58.1 (K), J22.4, U9.19 (OB2); also elsewhere on the board
/Motor Z/SS: U9.3 (CSN_CFG3); also elsewhere on the board
/Motor Z/STEP: U9.8 (STEP); also elsewhere on the board
GND: C52.2, C54.2, C56.2, C57.2, C58.2, C59.2, C60.2, C61.2, C63.2, C65.2, C66.2, C67.2, C68.2, C69.2, C70.2, C72.2, C74.2, C75.2, C76.2, C77.2, C78.2, D43.2 (A), D45.2 (A), D47.2 (A), D49.2 (A), D52.2 (A), D54.2 (A), D56.2 (A), D58.2 (A), D61.2 (A), D63.2 (A), D65.2 (A), D67.2 (A), R50.2, R51.1, R54.2, R55.1, R58.2, R59.1, U8.1 (TST_MODE), U8.2 (CLK), U8.13 (GNDP), U8.24 (DCEN_CFG4), U8.32 (GNDA), U8.48 (GNDP), U8.49 (GND-PAD), U9.1 (TST_MODE), U9.2 (CLK), U9.13 (GNDP), U9.24 (DCEN_CFG4), U9.32 (GNDA), U9.48 (GNDP), U9.49 (GND-PAD), U10.1 (TST_MODE), U10.2 (CLK), U10.13 (GNDP), U10.24 (DCEN_CFG4), U10.32 (GNDA), U10.48 (GNDP), U10.49 (GND-PAD); also elsewhere on the board
unnamed: C53.2, U8.38 (VCP)
unnamed: C55.1, U8.35 (CPO)
unnamed: C55.2, U8.37 (CPI)
unnamed: C59.1, U8.33 (5VOUT)
unnamed: C62.2, U9.38 (VCP)
unnamed: C64.1, U9.35 (CPO)
unnamed: C64.2, U9.37 (CPI)
unnamed: C68.1, U9.33 (5VOUT)
unnamed: C71.2, U10.38 (VCP)
unnamed: C73.1, U10.35 (CPO)
unnamed: C73.2, U10.37 (CPI)
unnamed: C77.1, U10.33 (5VOUT)
unnamed: R50.1, U8.44 (BRA)
unnamed: R51.2, U8.17 (BRB)
unnamed: R54.1, U9.44 (BRA)
unnamed: R55.2, U9.17 (BRB)
unnamed: R58.1, U10.44 (BRA)
unnamed: R59.2, U10.17 (BRB)
VDD3V3: C52.1, C61.1, C70.1, D41.2 (A), D50.2 (A), D59.2 (A), U8.10 (VCC_IO), U9.10 (VCC_IO), U10.10 (VCC_IO); also elsewhere on the board
VDD5V: C56.1, C65.1, C74.1, R52.1, R53.1, R56.1, R57.1, R60.1, R61.1, U8.34 (VCC), U9.34 (VCC), U10.34 (VCC); also elsewhere on the board
VDD_PWR: C53.1, C54.1, C57.1, C58.1, C60.1, C62.1, C63.1, C66.1, C67.1, C69.1, C71.1, C72.1, C75.1, C76.1, C78.1, D41.1 (K), D42.1 (K), D44.1 (K), D46.1 (K), D48.1 (K), D50.1 (K), D51.1 (K), D53.1 (K), D55.1 (K), D57.1 (K), D59.1 (K), D60.1 (K), D62.1 (K), D64.1 (K), D66.1 (K), U8.21 (VS), U8.39 (VSA), U8.40 (VS), U9.21 (VS), U9.39 (VSA), U9.40 (VS), U10.21 (VS), U10.39 (VSA), U10.40 (VS); also elsewhere on the board

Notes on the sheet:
Motor controller
Motor connection
Max RMS 1.64A
Place as close as possible to pins!
Bypass capacitors

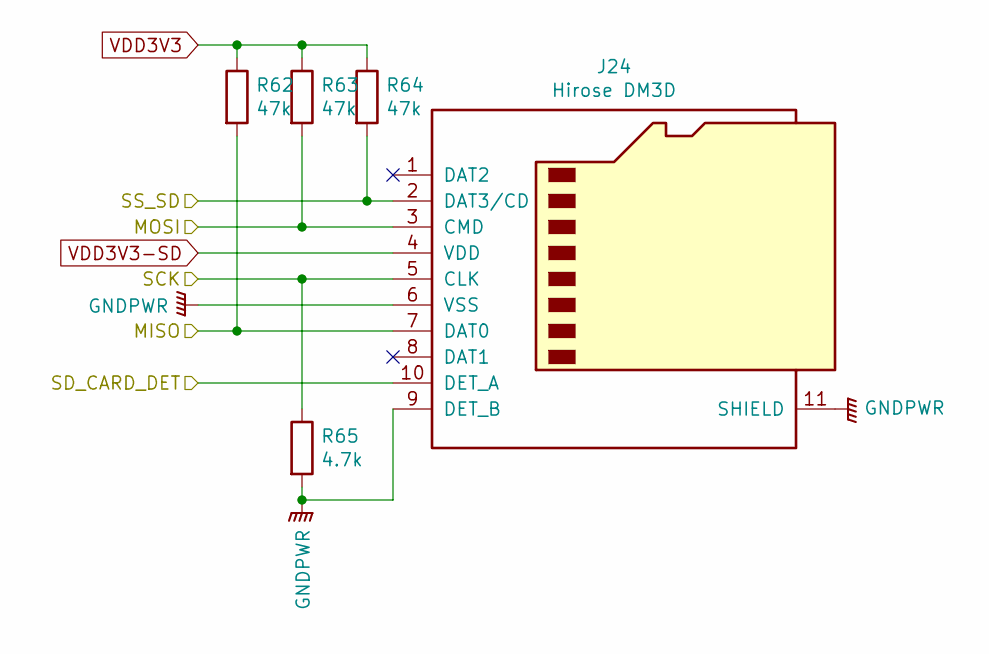
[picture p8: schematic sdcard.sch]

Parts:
J24: Hirose DM3D; microSD_HC_Hirose_DM3D-SF
R62, R63, R64: 47k; R_0603_1608Metric
R65: 4.7k; R_0603_1608Metric

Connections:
/MCU/MISO: J24.7 (DAT0), R62.2; also elsewhere on the board
/MCU/MOSI: J24.3 (CMD), R63.2; also elsewhere on the board
/MCU/SCK: J24.5 (CLK), R65.1; also elsewhere on the board
/MCU/SD_CARD_DET: J24.10 (DET_A); also elsewhere on the board
/MCU/SS_SD: J24.2 (DAT3/CD), R64.2; also elsewhere on the board
GND: J24.6 (VSS), J24.9 (DET_B), J24.11 (SHIELD), R65.2; also elsewhere on the board
VDD3V3: R62.1, R63.1, R64.1; also elsewhere on the board
VDD3V3-SD: J24.4 (VDD); also elsewhere on the board

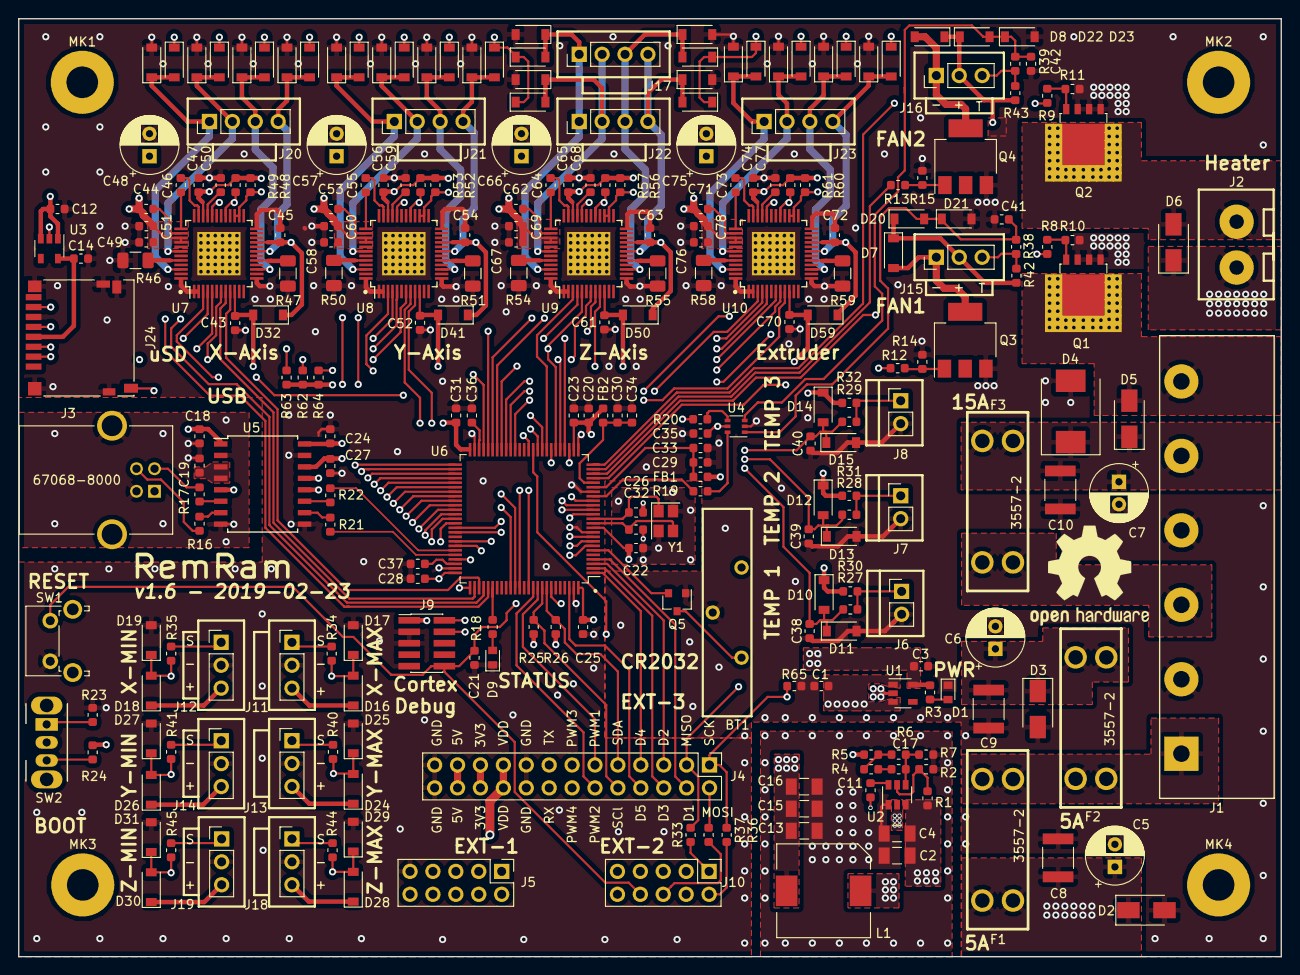
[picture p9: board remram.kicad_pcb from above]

Board: 4 copper layers, 140.0 x 104.0 mm, 264 parts (0 on the bottom side), 173 nets.

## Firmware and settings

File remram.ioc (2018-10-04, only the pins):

Mcu.UserName=STM32F765VITx
PA0/WKUP.GPIO_Label=PWM_FAN1
PA0/WKUP.Signal=S_TIM5_CH1
PA1.GPIO_Label=PWN_BED
PA1.Signal=S_TIM5_CH2
PA10.GPIO_Label=USART_RX
PA10.Signal=USART1_RX
PA11.GPIO_Label=MCU_DD-
PA11.Signal=USB_OTG_FS_DM
PA12.GPIO_Label=MCU_DD+
PA12.Signal=USB_OTG_FS_DP
PA13.GPIO_Label=SWDIO
PA13.Signal=SYS_JTMS-SWDIO
PA14.GPIO_Label=SWCLK
PA14.Signal=SYS_JTCK-SWCLK
PA15.GPIO_Label=X_STEP
PA15.Signal=S_TIM2_CH1_ETR
PA2.GPIO_Label=PWM_FAN2
PA2.Signal=S_TIM5_CH3
PA3.GPIO_Label=PWM_HEAT
PA3.Signal=S_TIM5_CH4
PA4.GPIO_Label=FAN_SPEED1
PA4.Signal=ADCx_IN4
PA5.Signal=SPI1_SCK
PA6.Signal=SPI1_MISO
PA7.Signal=SPI1_MOSI
PA9.GPIO_Label=USART_TX
PA9.Signal=USART1_TX
PB0.GPIO_Label=SS_Y
PB0.Signal=GPIO_Output
PB1.GPIO_Label=SS_X
PB1.Signal=GPIO_Output
PB10.GPIO_Label=Z_STEP
PB10.Signal=S_TIM2_CH3
PB11.GPIO_Label=E_STEP
PB11.Signal=S_TIM2_CH4
PB12.GPIO_Label=X_MIN
PB12.Signal=GPIO_Input
PB13.GPIO_Label=X_MAX
PB13.Signal=GPIO_Input
PB14.GPIO_Label=Y_MIN
PB14.Signal=GPIO_Input
PB15.GPIO_Label=Y_MAX
PB15.Signal=GPIO_Input
PB2.GPIO_Label=SS_SDLCD
PB2.Signal=GPIO_Output
PB3.GPIO_Label=Y_STEP
PB3.Signal=S_TIM2_CH2
PB4.GPIO_Label=PWM_EXT1
PB4.Signal=S_TIM3_CH1
PB5.GPIO_Label=PWM_EXT2
PB5.Signal=S_TIM3_CH2
PB6.GPIO_Label=SCL
PB6.Signal=I2C1_SCL
PB7.GPIO_Label=SDA
PB7.Signal=I2C1_SDA
PC0.GPIO_Label=THERM_1
PC0.Signal=ADCx_IN10
PC1.GPIO_Label=THERM_2
PC1.Signal=ADCx_IN11
PC10.GPIO_Label=X_DIR
PC10.Signal=GPIO_Output
PC11.GPIO_Label=X_DIAG
PC11.Signal=GPIO_Input
PC12.GPIO_Label=X_EN
PC12.Signal=GPIO_Output
PC13.GPIO_Label=SD_CARD_DET
PC13.Signal=GPIO_Output
PC14/OSC32_IN.GPIO_Label=BTN_EN1
PC14/OSC32_IN.Signal=GPIO_Input
PC15/OSC32_OUT.GPIO_Label=BTN_EN2
PC15/OSC32_OUT.Signal=GPIO_Input
PC2.GPIO_Label=THERM_3
PC2.Signal=ADCx_IN12
PC3.GPIO_Label=FAN_SPEED2
PC3.Signal=ADCx_IN13
PC4.GPIO_Label=SS_E
PC4.Signal=GPIO_Output
PC5.GPIO_Label=SS_Z
PC5.Signal=GPIO_Output
PC6.GPIO_Label=LCD_BEEPER
PC6.Signal=GPIO_Output
PC7.GPIO_Label=BTN_ENC
PC7.Signal=GPIO_Input
PC8.GPIO_Label=PWM_EXT3
PC8.Signal=S_TIM3_CH3
PC9.GPIO_Label=PWM_EXT4
PC9.Signal=S_TIM3_CH4
PD0.GPIO_Label=STATUS_LED
PD0.Signal=GPIO_Output
PD10.GPIO_Label=LCD_D7
PD10.Signal=GPIO_Output
PD11.GPIO_Label=LCD_D6
PD11.Signal=GPIO_Output
PD12.GPIO_Label=LCD_D5
PD12.Signal=GPIO_Output
PD13.GPIO_Label=LCD_D4
PD13.Signal=GPIO_Output
PD14.GPIO_Label=LCD_EN
PD14.Signal=GPIO_Output
PD15.GPIO_Label=LCD_RS
PD15.Signal=GPIO_Output
PD4.GPIO_Label=Y_EN
PD4.Signal=GPIO_Output
PD5.GPIO_Label=Y_DIAG
PD5.Signal=GPIO_Input
PD6.GPIO_Label=Y_DIR
PD6.Signal=GPIO_Output
PD8.GPIO_Label=Z_MIN
PD8.Signal=GPIO_Input
PD9.GPIO_Label=Z_MAX
PD9.Signal=GPIO_Input
PE1.GPIO_Label=EXT_D5
PE1.Signal=GPIO_Output
PE10.GPIO_Label=E_DIR
PE10.Signal=GPIO_Output
PE11.GPIO_Label=E_EN
PE11.Signal=GPIO_Output
PE12.GPIO_Label=E_DIAG
PE12.Signal=GPIO_Input
PE13.GPIO_Label=Z_DIR
PE13.Signal=GPIO_Output
PE14.GPIO_Label=Z_DIAG
PE14.Signal=GPIO_Output
PE15.GPIO_Label=Z_EN
PE15.Signal=GPIO_Output
PE2.GPIO_Label=EXT_D4
PE2.Signal=GPIO_Output
PE3.GPIO_Label=EXT_D3
PE3.Signal=GPIO_Output
PE4.GPIO_Label=EXT_D2
PE4.Signal=GPIO_Output
PE5.GPIO_Label=EXT_D1
PE5.Signal=GPIO_Output
PE7.GPIO_Label=SS_SD
PE7.Signal=GPIO_Output
PH0/OSC_IN.Signal=RCC_OSC_IN
PH1/OSC_OUT.Signal=RCC_OSC_OUT

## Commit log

2018-05-11 First commit of the new STM32 printer controller.
    [MCU.sch, connectors.sch, fans.sch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]
2018-05-12 Changed PCB.
    - Added MOSFET, connectors sheet
    - Changed MCU and power sheet
    - Reorganised sheets
    [MCU.sch, connectors.sch, fans.sch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]
2018-05-12 Removed some resistors for mosfets.
    I don't think they are needed.
    Also added some missing footprints.
    [mosfets.sch]
2018-05-13 Added PD registors on MOSFET gates.
    [mosfets.sch]
2018-05-13 Changed some sheets and added LICENCE.
    [MCU.sch, connectors.sch, mosfets.sch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]
2018-05-13 Finished first draft of the schematics.
    [MCU.sch, connectors.sch, mosfets.sch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]
2018-05-13 Fixed bugs found with ERC.
    [MCU.sch, connectors.sch, mosfets.sch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]
2018-05-13 Added missing foorprints.
    [MCU.sch, connectors.sch, power.sch]
2018-05-13 Fixed annotations and assignment errors.
    [MCU.sch, connectors.sch, mosfets.sch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]
2018-05-14 Saving work in progress.
    Every component now has a 3D mode.
    [MCU.sch, connectors.sch, mosfets.sch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]
2018-05-15 Removed logic level converter. Changed LDO.
    [MCU.sch, connectors.sch, mosfets.sch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]
2018-05-15 First try to layout a TMC driver.
    [remram.kicad_pcb]
2018-05-15 Layout for USB isolation.
    [remram.kicad_pcb]
2018-05-15 Finished TMC2130 placement.
    Motor sheets is now instanced. That way I simply could use
    a KiCad plugin to duplicate the layout in Pcbnew.
    [MCU.sch, connectors.sch, mosfets.sch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]
2018-05-16 Finished placement. Currently routing last paths.
    [MCU.sch, connectors.sch, motor.sch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]
2018-05-16 Added the secnd Z connection.
    [MCU.sch, connectors.sch, motor.sch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]
2018-05-16 First PCB version that is fully placed and routed.
    [MCU.sch, motor.sch, remram.kicad_pcb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]
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2018-05-17 Fixed some connections.
    [MCU.sch, remram.kicad_pcb]
2018-05-17 Added a symbols text to silk screen.
    [remram.kicad_pcb]
2018-05-17 Reworked some traces for better layout.
    This will also come in handy, when we add more external
    connections (10 to 20pin external).
    [MCU.sch, connectors.sch, mosfets.sch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]
2018-05-17 Re-routed some traces.
    General cleanup.
    [MCU.sch, motor.sch, remram.kicad_pcb]
2018-05-17 Reworked some traces and labels.
    [MCU.sch, connectors.sch, mosfets.sch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]
2018-05-17 Added missing labels.
    [remram.kicad_pcb]
2018-05-17 First draft of RemRam.
    I added a 20 pin expansion connector with the following pins:
    - SPI
    - I2C
    - USART
    - 4x PWM
    - 4x GPIO
    [MCU.sch, connectors.sch, mosfets.sch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]
2018-05-18 v0.2 of PCB.
    After some feedback, we changed following:
    - Switched FAN VDD from 24 to 5V.
    - FAN now have a ADC pin for speed sensing.
    - Expanded EXP-3 connector to 26 pin
    - Included 24V VDD.
    - Could be used to connect up to two
    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
    [MCU.sch, connectors.sch, mosfets.sch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]
2018-05-18 Corrected MK3 hole and added some measurements.
    [remram.kicad_pcb]
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2018-05-18 Added a yellow status LED.
    [MCU.sch, motor.sch, remram.kicad_pcb]
2018-05-18 Added missing change in MCU definition file.
    [remram.ioc]
2018-05-19 Changed the LED resistors to real values.
    [MCU.sch, power.sch, remram.kicad_pcb]
2018-05-19 Changed ordering of parts. Version 0.4.
    [MCU.sch, connectors.sch, motor.sch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]
2018-05-19 Moved some ADC lines for better noise isolation.
    [remram.kicad_pcb]
2018-05-19 Removed USART1 CK pin and added another digial pin.
    STM32duino doesn't seem to support USART. So I will only
    implement the UART pins.
    [MCU.sch, connectors.sch, remram.kicad_pcb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]
2018-05-19 Reworked the ground plane for better ADC isolation.
    [remram.kicad_pcb]
2018-05-20 Changed LED to sane values. Updated diodes. v0.5.
    [MCU.sch, mosfets.sch, power.sch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]
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2018-06-24 Change DC-DC layout
    The ripple on the 5V and 3V3 rail was too high (360mV).
    In an attempt to reduce the RF and HF noise, I changed the layout
    to a more compact one. I also added a third 22uF output capacitor
    behind the inductor to lower ESR. I also added a 100nf input
    capacitor to combat HF noise, as recommended in the datasheet.
    The BOM needs to be updated in such a way, that we specificly
    choose low ESR resistors.
    [MCU.sch, connectors.sch, mosfets.sch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]
2018-06-24 Fix the SWD connector
    I screwed up and switched the SWDIO and SWCLK pins.
    [connectors.sch, remram.kicad_pcb]
2018-06-24 Add information about debugging in README.md
    People might want to use the Cortex Debug Header to program and
    debug the STM32.
    I added information about the supported mode (only SWD) and missing
    SWO pin (So no SWO tracing / console output).
    We had to sacrifice thw SWO pin for a PWM output. This shouldn't
    matter much, since step-by-step debugging is working finde
    and Marlin doesn't use the SWO output anyhow.
2018-06-27 Add diodes and PU to endstops and fans (SCH only)
    For extra protection and PU, we added some diodes and a
    pull up resistor to the endstops and the fan tachometer.
    [connectors.sch, motor.sch, remram.kicad_pcb]
2018-06-27 Change 1k resistors to 4.7k. Update Symbols
    Had to update the symbols to the right library again, since
    Kicad Nightly changed their library order.
    Also changed the 1k resistors to 4.7k to unify resistors and
    also upped the PU to a weaker value.
    [BOM - RemRam v0.5.csv, MCU.sch, connectors.sch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]
2018-06-27 Added protection diodes to TMC2130
    Diode on IO voltage protects chip to only accept command when
    motor voltage is present.
    Clamping diodes on motor outputs are for inductive loads.
    [MCU.sch, connectors.sch, motor.sch]
2018-06-27 Add missing MOSFET footprint
    [MCU.sch, motor.sch]
2018-06-28 Switch GND and VDD_PWR on EXT-3
    Just to make updating over UART a little bit safer.
    [connectors.sch, motor.sch]
2018-06-30 Rework the PCB after feedback
    This design incooperated following changes:
    * Better power distribution
    * Diodes for driver, endstops and fan tachometer
    * Mounting holes not grounded and size 3.5mm
    * Better EXT3 header description
    * EXT1 and EXT2 footprint for normal 2.54 header
    * Reverse voltage protection for the battery
    * PU for driver enable pin
    * Better crystal placement
    * 2 sided board layout for better routing and
    placement
    [connectors.sch, motor.sch, power.sch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]
2018-06-30 Fix some traces
    Some on the 3V3 rail had some weird
    connection which I fixed.
    [remram.kicad_pcb]
2018-07-01 Fix PU on FAN RPM, Endstops and Grounding
    * Fixes too weak PU on RPM for fans
    * Simplified endstop setup
    * Grounding fixes:
    * GND below SPI bus
    * 3V3 LDO directly attached
    to main PWR source
    Fixes #20
    [MCU.sch, connectors.sch, mosfets.sch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]
2018-07-01 Add a P MOSFET to protect the TPS54308
    Since I fried two TPS54308 already, I think it would
    be best to implement a reverse voltage protection
    before the TPS that provides the 5V rail.
    To reuse parts, I also switches the battery protection
    P MOSFET to the same part.
    [MCU.sch, connectors.sch, mosfets.sch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]
2018-07-01 Chang battery holder
    This battery holder is more widely available.
    [MCU.sch, remram.kicad_pcb]
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2018-07-03 Fix minor cosmetic issues
    [remram.kicad_pcb]
2018-07-04 Revert back to IRLML6401 for battery protection
    I reverted back to use the IRLML, since the gate-source threshhold
    coltage for the other P MOSFET was not low enough to always work
    inside the battery voltage.
    [MCU.sch, remram.kicad_pcb]
2018-07-04 Updat the BOM for v1.0
    Updated BOM with mouser and digikey order numbers.
    [BOM - RemRam v0.5.csv, BOM - RemRam v1.0.csv]
2018-07-05 Add compability for TPS54302
    Since the TPS54308 is often not available, we added the
    option to also use the TPS54038. This commit added a lot
    of components and changed the CSV.
    [BOM - RemRam v1.0.csv, MCU.sch, connectors.sch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]
2018-07-06 Optimize BOM for v1.0
    * Add alternative for heater / heatbed N-MOSFET
    * Changed 100k resistor for more cost effective variant
    [BOM - RemRam v1.0.csv]
2018-07-26 Add Schmitt Trigger for fan tachometer
    The fan tachometer is too noise for the STM32F7 3.3V IO.
    We need to add a Schmitt Trigger to have a better noise handling
    and gain more low/high margin.
    Also some minor silkscreen adjustments. Backward compatible
    with v1.0.wq
    [MCU.sch, connectors.sch, remram.kicad_pcb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]
2018-07-26 Change tachometer resistors to 4.7k and update BOM
    To better filter the tachometer signal, we had to increase the
    reistors of the tachometer RC filter and PU to 4.7k.
    This commit also updates the BOM for all changed since v1.0.wq
    [BOM - RemRam v1.0.csv, BOM - RemRam v1.1.csv, connectors.sch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]
2018-07-29 Switch BTN_ENC1 & BTN_ENC2
    Simple cosmetic change. The connector has them switched.
    [MCU.sch, connectors.sch, remram.kicad_pcb]
2018-08-25 Add series resistors to EXT-2 SPI lines
    To help with noisy ribbon cables and SD card communication we
    add three 100 ohm resistors in series for the SPI pins.
    [connectors.sch, remram.kicad_pcb]
2018-10-03 Plain GND plane, new Debug Header, KILL PIN now RESET
    [MCU.sch, connectors.sch, power.sch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]
2018-10-03 Place all components on top and better routing
    [remram.kicad_pcb]
2018-10-04 Add micro SD card reader and finished GND stitching
    Just to be safe, the SD card reader got it's own LDO.
    [MCU.sch, connectors.sch, mosfets.sch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]
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2018-10-04 New item designations and fixes some small manufacturing issues
    [MCU.sch, connectors.sch, mosfets.sch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]
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2018-10-07 Small cosmetic changes and fixed BOM.
    [BOM.ods, remram.kicad_pcb]
2018-11-10 Fixes of v1.3 errors
    * Fixed missing GND connection for SD card detect
    * Optimized solder mask clearance from 0.2 to 0.05
    * Changed 3.3V LDO
    [BOM.ods, power.sch, remram.kicad_pcb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]
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2018-11-24 Finalised the silkscreen and fixed one copper pure
    Copper pure fixed:
    * VCC connection on USB isolation chip
    Silkscreen fix:
    * Orientation marker on connectors
    [remram.kicad_pcb]
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2019-01-12 Fixed BOM and some footprint issues.
    [BOM.ods, remram.kicad_pcb, sdcard.sch]
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2019-02-23 Add PD for SPI SCK and some footprint fixes
    Footprint fixes are mainly orientation markings.
    PD needed for missbehaving Marlin firmware.
    [BOM.ods, MCU.sch, connectors.sch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]
